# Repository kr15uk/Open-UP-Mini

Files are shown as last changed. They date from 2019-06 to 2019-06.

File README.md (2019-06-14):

# Open-UP-Mini

UP Mini is brilliant well tuned ABS machine and for most people this conversion will bring more pain than benefit.

Reasons behind the conversion:

1. I had 4x other machines running Marlin and my slicer of choice was Cura.

2. I've started experimenting with PC-ABS and PC and wasn't 100% satisfied due to low bed/chamber temperatures for these materials.

Bed reaches only 60degree C max hence it's not regulated (it has some kind of temp sensing cutout diode soldered underneath - not familiar with this technology)
If you want to install chamber heaters you will require to have separate controller etc - pain.

3. Due to declining availability of UP replacement nozzles I had a plan to potentially upgrade this machine to more generic E3D offerings (potentially Titan Aqua)

So far I have replaced electronics with AliExpress BIQU KFB 2.0 board (space for additional mosfet board if going chamber heater route), moded bed to go over 60degree C and added thermistor - the rest is kept as stock as possible.

So far I've been unsuccessful:

1. Sensing hotend thermistor, it's not regular thermistor nor PT100 - so save some troubleshooting time I've simply strapped with capton tape regular NTC onto the heater block (temporary solution, for almost a year now :) )

2. Find a use case for UP front button and LED so it's not wired

3. Design LCD mount

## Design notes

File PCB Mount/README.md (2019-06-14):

# BIQU KFB 2.0 replacement board

Went with this board hence it was fairly cheap, decent set of IO, JST connectors so I can plug existing cables without modifications (no need to re-crimp connectors and board has perfect USB port location so it can be fitted nicely without adding cable extensions or so).

Under consideration also had these boards but chose not to go with them:

MKS Gen board - has slightly different layout so cable extensions or case modifications will be required.

MKS S Gen - 32bit board is not necessary for cartesian machine.

RAMPS - too thick for lid to come back on + requires connector re-crimping.

If you have suggestion of quality board with similar form factor and JST connectors - happy to reconsider.

Motion wiring is pretty buch straight forward apart from typical UP machine X and Y axis mixup (X = Y and Y is X, looks like they come from CNC background...)

Hotend, Extruder and Bed wiring (ribbon connector ones) info you can find in their folders.

PCB Mount also includes place for additional mosfet if you desire to run chamber heaters.

DC jack is generic DC jack, like the one you can find on Arduino Mega boards. Haven't checked AMP rating but UP machine has quite low power rated components so I've assumed it's good enough - please correct me if I'm wrong.

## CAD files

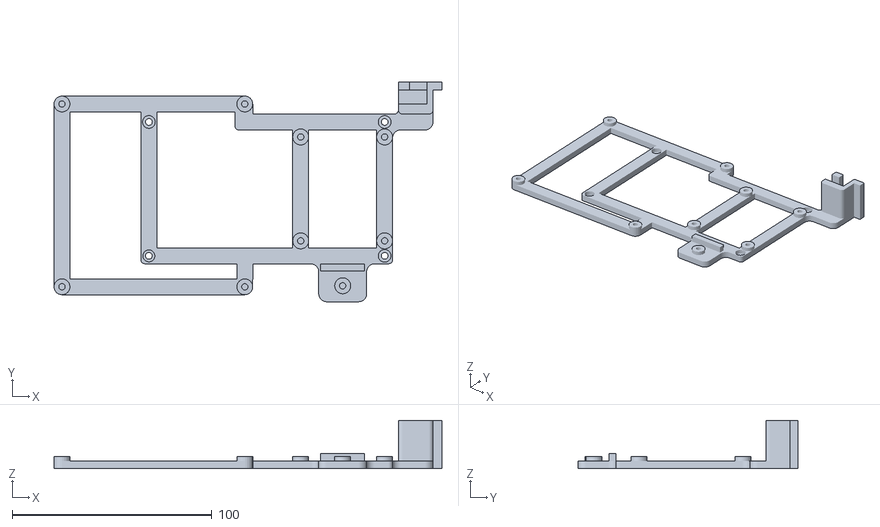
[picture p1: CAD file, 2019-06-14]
PCB Mount/PCB Mount v1.0.stl
194.2 x 109.9 x 24.2

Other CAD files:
PCB Mount/PCB Mount v1.0.skp
